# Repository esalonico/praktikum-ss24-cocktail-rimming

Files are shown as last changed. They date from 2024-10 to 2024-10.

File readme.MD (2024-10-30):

# Automated Cocktail Rimming System

**SS24 - Advanced Practical Course "Sustainable Process Automation: Humans, Software and the Mediator Pattern (IN2130, IN2106, IN4303)"**

An automated solution to streamline the process of rimming cocktail glasses, enhancing efficiency, consistency, and reducing resource waste, while at the same time praciting different skills like process management, 3D printing, electronics and process design/execution.

## Video

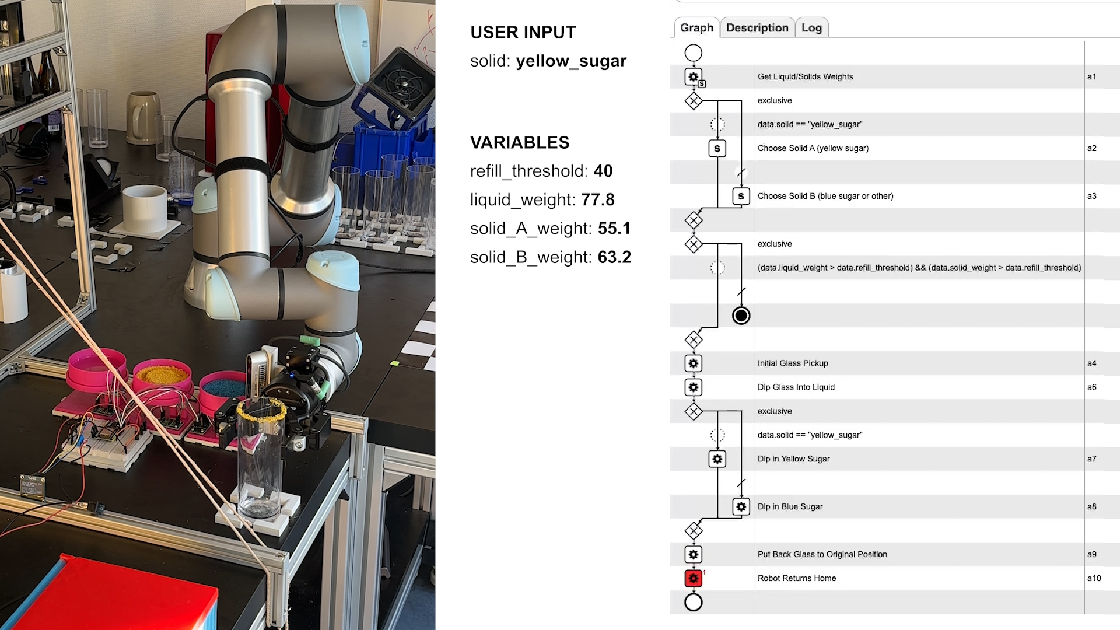
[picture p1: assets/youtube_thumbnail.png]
YouTube Video Thumbnail (https://youtu.be/M-wNSkutfYI)

*Click on the preview image to play the video on YouTube, or visit this URL: <https://youtu.be/M-wNSkutfYI>*

## Project Overview

### Main Idea

The goal of this project is to automate the process of rimming a cocktail glass. This involves dipping the glass first into a liquid (often lemon juice or syrups) and subsequently into a coating (such as sugar or salt) to enhance the presentation and flavor of the cocktail.

The project aims to solve the problem of manually rimming cocktail glasses by ensuring a consistent and efficient application of the sugar or salt coating. In practical use, this automation improves cocktail preparation times and minimizes waste by precisely controlling the amount of liquid and solid applied. Additionally, it provides the ability to track quantities used via integrated weighing sensors.

## Technical Summary

The project consists of three main components:

- **Robot**: From [Universal Robots](https://www.universal-robots.com/) for ultra precise and repeatable movements.
- **Hardware**: Custom-designed, 3D-printed components. *[(Go to section)](#hardware)*
- **Software**: Composed of CPEE (Cloud Process Execution Engine), ESP32 code, and a custom web server. *[(Go to section)](#software)*

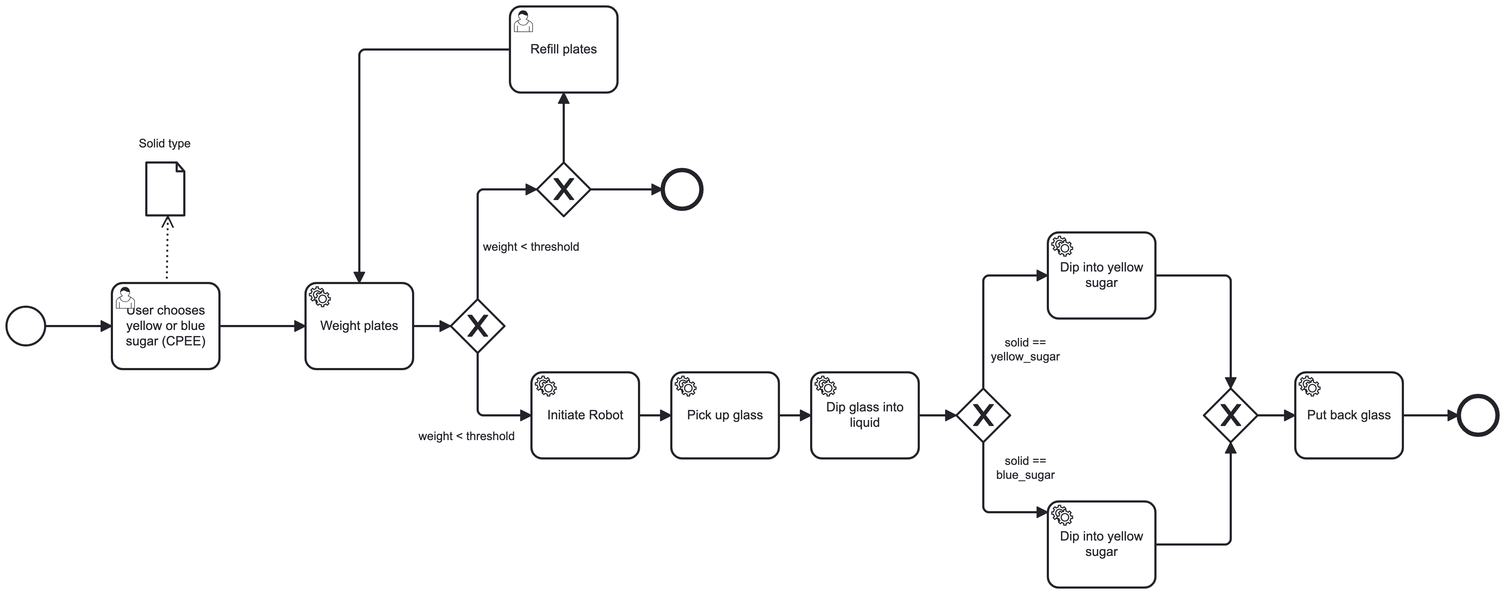
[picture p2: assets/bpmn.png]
BPMN
  
*High-level overview of the cocktail rimming process in BPMN.*

## Hardware

The hardware includes three identical stations to store and weigh the substances (one for the liquid and two for the solids). These stations connect to a central unit containing all circuits, the ESP32 microcontroller, an ON/OFF switch, and an OLED display.

This modular design facilitates straightforward scalability in the future.

### Components

- **In each station (3 total):**
  - **3D Printed Parts:**
    - Square base plate ([A](assets/3d_parts/A.stl))
    - Supports for the load cell ([B](assets/3d_parts/B.stl), [C](assets/3d_parts/B.stl))
    - Circular base plate (as a base for the plate) ([D](assets/3d_parts/D.stl))
    - Main plate (for storing liquid/solids) ([E](assets/3d_parts/E.stl))
  - **Electronics:**
    - 5kg load cell
    - HX711 amplifier
- **Control Center:**
  - ESP32 microcontroller (with WiFi support)
  - OLED I2C display
  - ON/OFF switch (connected to a 5V power adapter)

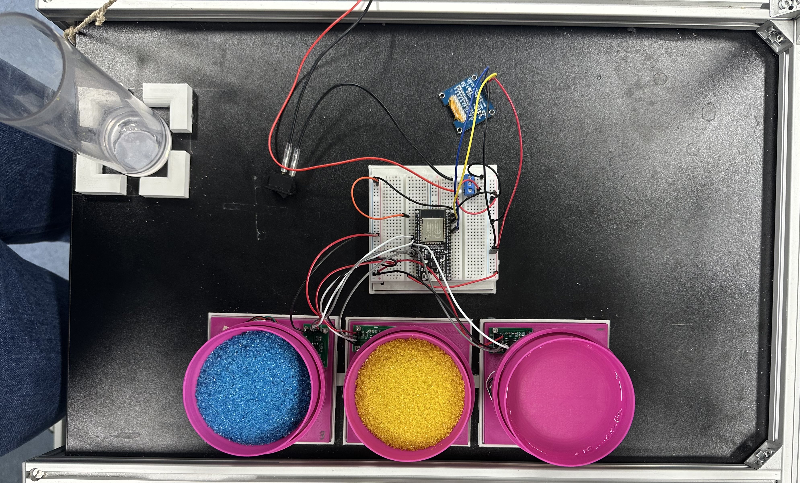
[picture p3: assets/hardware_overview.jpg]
Hardware Overview
  
*Hardware overview*

The custom 3D parts were designed using [Autodesk Fusion 360](https://www.autodesk.com/products/fusion-360/overview). Links to the `.stl` files for each component can be found above in the parts list.

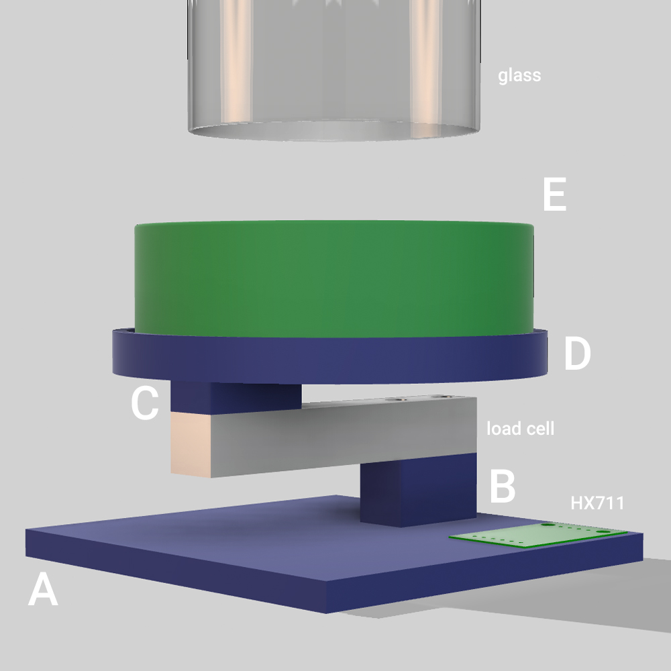
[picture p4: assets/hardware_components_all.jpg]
3D printed components
  
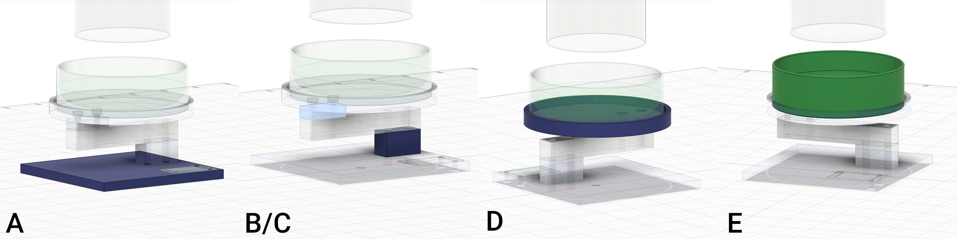
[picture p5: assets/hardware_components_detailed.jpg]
Detailed hardware components
  
*3D-printed hardware components.*

The design went through several iterations to find optimal solutions for various aspects such as load cell sensitivity, vibration motors to distribute sugar/salt (eventually discarded), and different plate sizes.

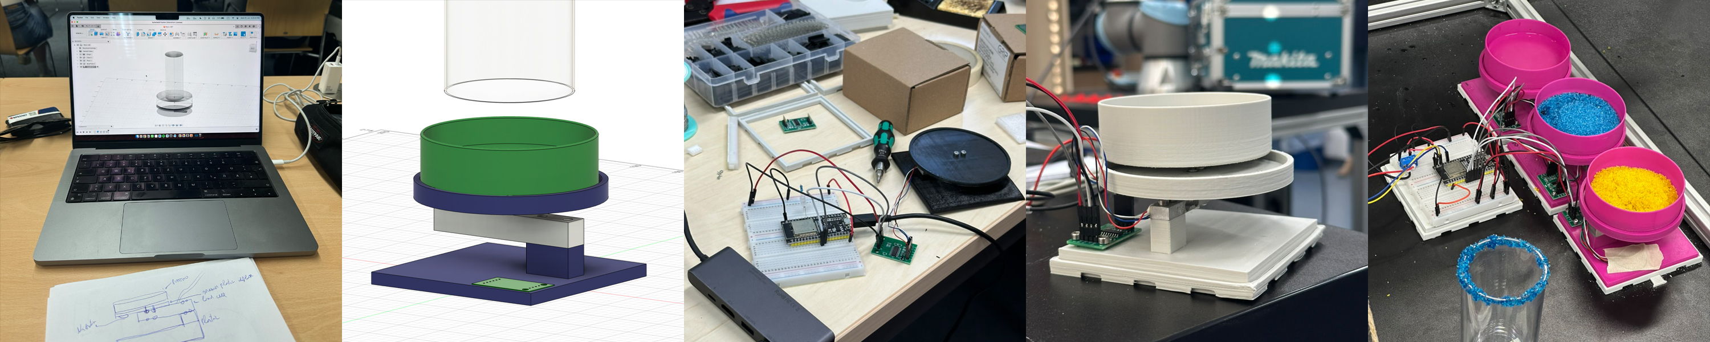
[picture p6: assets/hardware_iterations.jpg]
Iterations
  
*Multiple design iterations were necessary to achieve a working solution.*

Below is a diagram representation of the ESP32 pins and their connections.

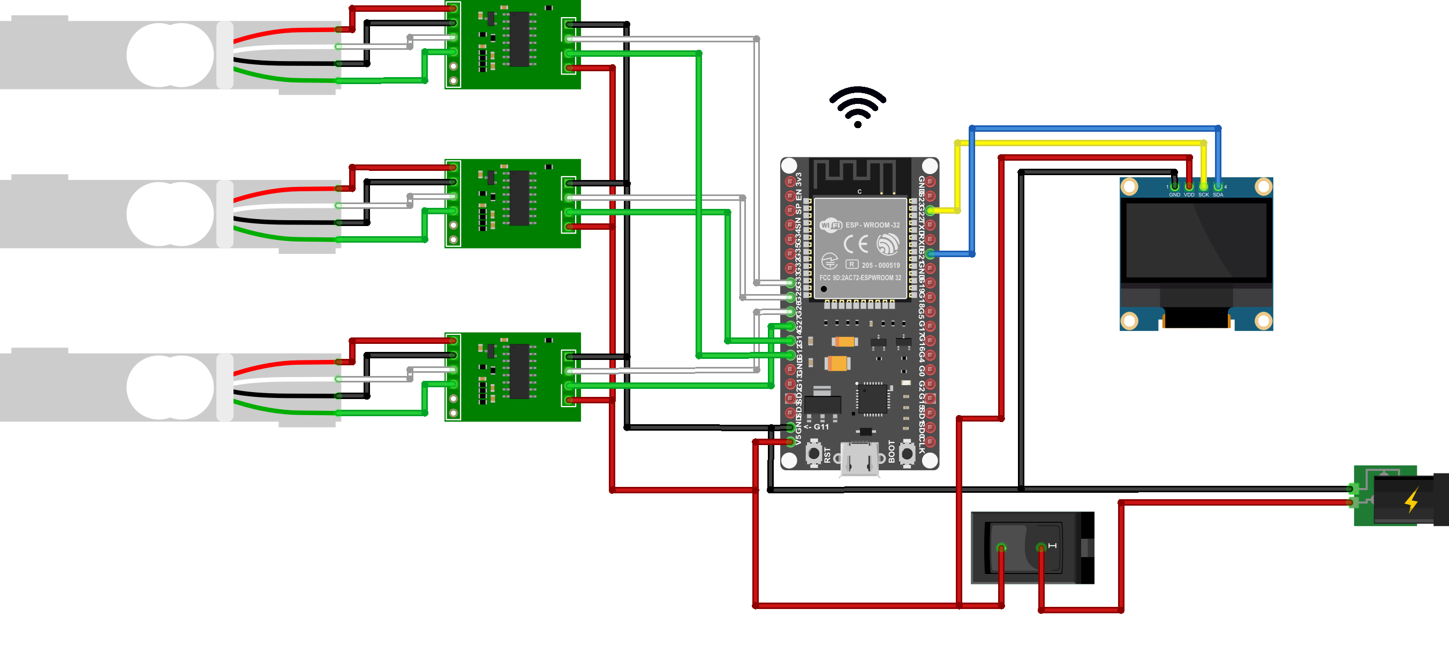
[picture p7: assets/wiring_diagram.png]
ESP32 Schematics
  
*Wiring diagram for the electronics connected to the ESP32.*

## Software

### Architecture

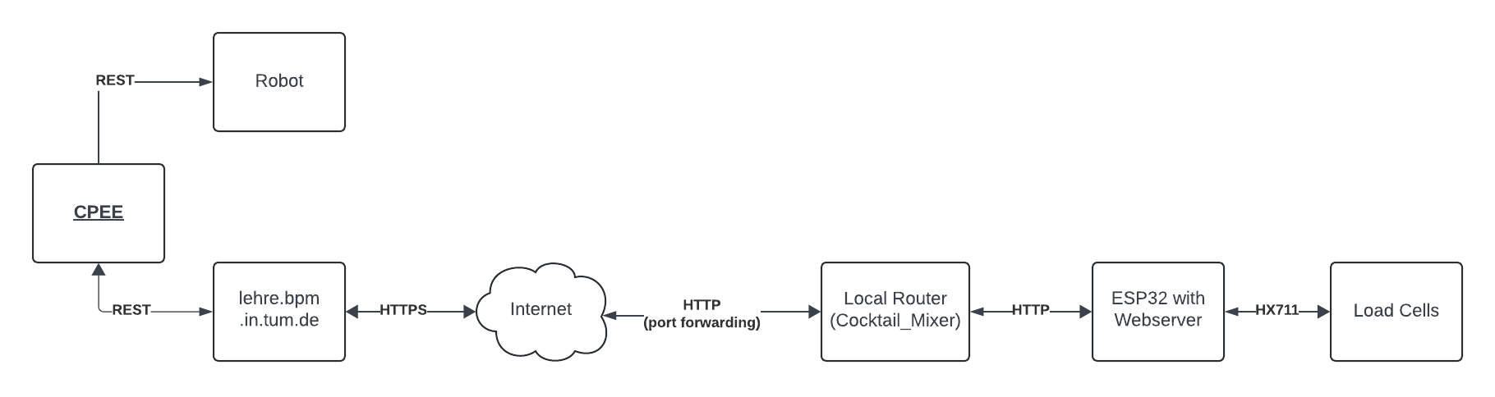
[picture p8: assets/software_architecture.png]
Architecture
  
*Architecture of all project components and their interactions.*

The software architecture includes the following main services:

- [**ESP32**](#esp-32): REST services between hardware and CPEE, web server, load cell configuration, and display management.
- [**CPEE**](#cpee-cloud-process-execution-engine): Process engine and orchestrator.
- **Robot**: Manages robotic actions to execute glass dipping sequences.
- [**WiFi Router**](#wifi-router): Makes the ESP32 web server accessible publicly.

#### ESP32

- **Purpose**: Provide a simple REST service to control and monitor the load cells (weight retrieval, status, calibration) and control the display (showing IP addresses for connecting to the web server).

The ESP32 uses an asynchronous web server (`AsyncWebServer`) to expose the routes. The endpoints are designed to guarantee isolation of data from the process, enabling them to be reused in various contexts with minimal dependencies.

##### API Documentation: GET `/weight`

- **Endpoint:**
  - **URL:** `{{WEBSERVER_IP}}/weight`
  - **Method:** `GET`
  - **Description:** Retrieves weight measurements (in grams) from all load cells connected to the ESP32 device.

##### **Response:**

- **Status Code:** `200 OK`
- **Content-Type:** `application/json`
- **Response Body:**
  
  ```json
  {
      "load_cells": [
          {
              "id": 1,
              "weight": 1.8
          },
          {
              "id": 2,
              "weight": 0.1
          },
          {
              "id": 3,
              "weight": 0.7
          }
      ]
  }
  ```

##### **Notes:**

- Replace `{{WEBSERVER_IP}}` with the IP address or domain name of the ESP32 web server.
- Weights are returned in grams with up to one decimal precision.

Additional routes are designed in `src/routes.cpp`. A Postman collection of all endpoints is available in [`assets/postman_collection.json`](assets/postman_collection.json).

Utilities for tasks such as load cell calibration, display testing, and HX711 debugging are available in the `utils` folder.

The project is built and managed via [PlatformIO](https://platformio.org/).

#### CPEE (Cloud Process Execution Engine)

- **Purpose**: Create a modular and well-structured process that coordinates the interactions between the user, sensors (load cells), and the robot.

Refer to the [video](#video) for a graphical representation of the process. Multiple CPEE components, such as service calls, script elements, and decisions, were used to fully utilize CPEE's capabilities.

#### WiFi Router

- **Purpose**: Expose the ESP32 web server endpoints to the internet.

Since modifying the routing configuration on eduroam is not possible, an additional router is used. The ESP32 connects to this router, which assigns a static local IP (192.168.0.125). Port forwarding is then set up to make port 80 accessible online, redirecting it to the ESP32's services.

The script [`utils/server_api.php`](utils/server_api.php) is used on the public server to forward requests to the ESP32.

## How to Run

- **ESP32 Setup:**
  - Create a file `data/wifi_credentials.txt` following the format in `data/SAMPLE_wifi_credentials.txt`.
  - In `main.cpp`, adjust:
    - Local IP address of the ESP32.
    - Public IP address or URL for accessing the web server.

- **Local Router Setup:**
  - Set up port forwarding for the ESP32's local IP address.

- **Public Server Setup:**
  - Upload `utils/server_api.php`.
  - Update the IP and port for the router.

## Challenges

### Personal Challenges

- Learning new skills including 3D modeling, 3D printing, soldering, electronics, and integrating these skills with robot commands.
- Optimizing the process engine based on lessons learned from the BPTM course.

### Technical Challenges

- Managing liquid and sugar refill (when below the threshold) using the robot.
- Ensuring even distribution of sugar/salt to avoid forming clumps (initially considered using a vibration motor).

## Future Implementations

- Use smaller load cells (e.g., less than 5kg) to better suit this application.
- Build an enclosure for the main unit.
- Add support for additional liquids/solids for a more modular design.
- Add debug/status displays for better monitoring.

---
**Author:** Emanuele Salonico | [emanuele.salonico@tum.de](mailto:emanuele.salonico@tum.de)

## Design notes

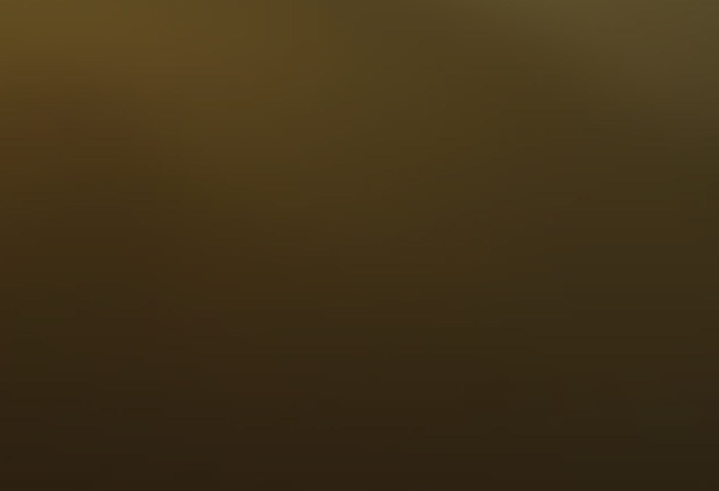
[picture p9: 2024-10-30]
assets/placeholder.png

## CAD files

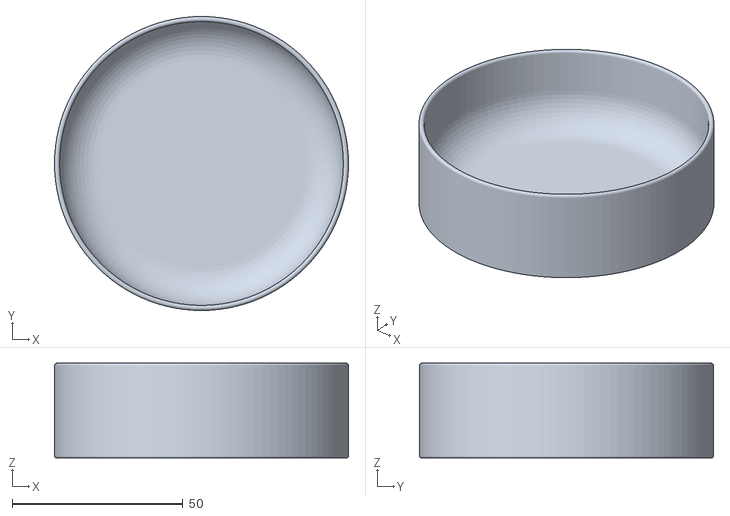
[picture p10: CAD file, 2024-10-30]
assets/3d_parts/E.stl
86.0 x 86.0 x 27.8

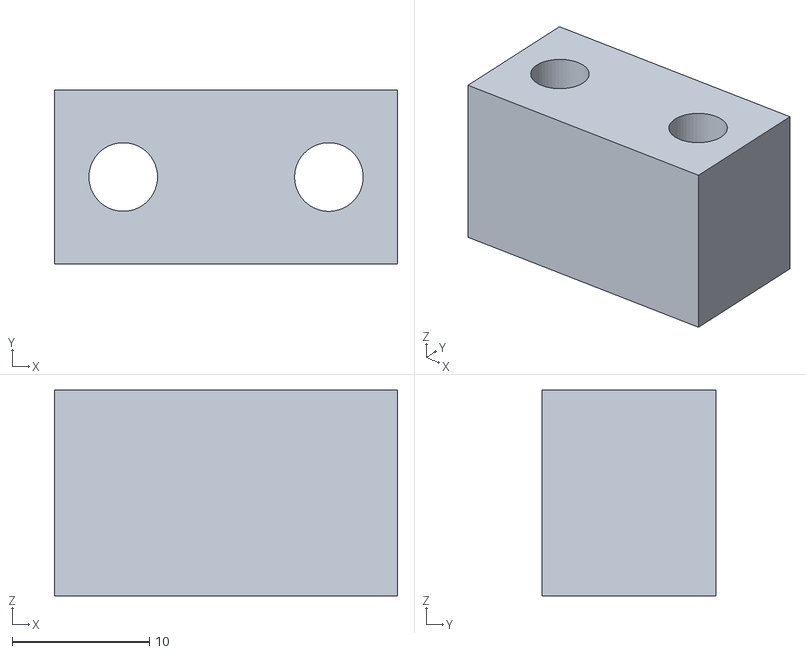
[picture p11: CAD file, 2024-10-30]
assets/3d_parts/B.stl
25.0 x 12.7 x 15.0

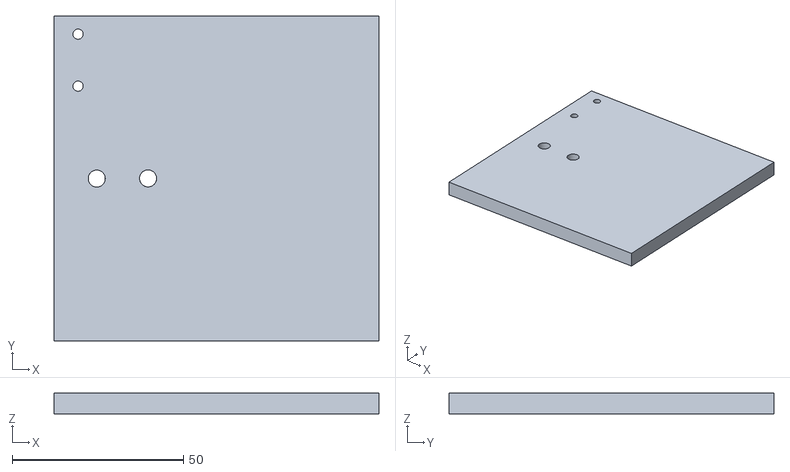
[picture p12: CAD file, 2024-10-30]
assets/3d_parts/A.stl
95.0 x 95.0 x 6.00

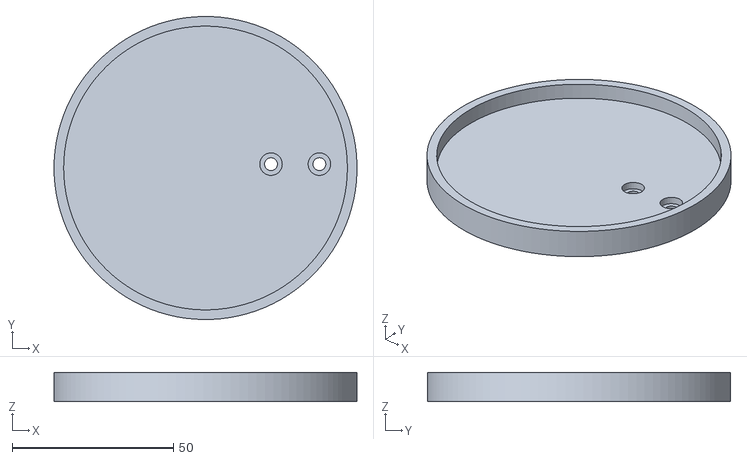
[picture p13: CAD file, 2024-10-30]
assets/3d_parts/D.stl
94.0 x 94.0 x 9.00

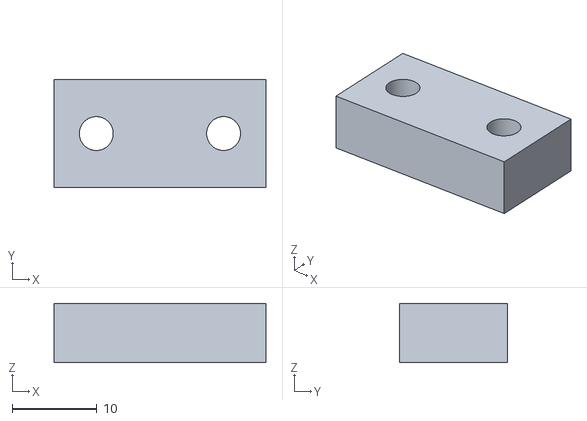
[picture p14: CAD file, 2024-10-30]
assets/3d_parts/C.stl
25.0 x 12.7 x 7.00

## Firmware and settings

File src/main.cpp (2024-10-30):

#include <Arduino.h>
#include <WiFi.h>
#include <AsyncTCP.h>
#include <ESPAsyncWebServer.h>
#include "FS.h"
#include "SPIFFS.h"
#include "HX711.h"
#include <Wire.h>
#include <Adafruit_GFX.h>
#include <Adafruit_SH1106.h>
#include "routes.h"

// Eduroam network credentials file path
const char *credentialsPath = "/wifi_credentials.txt";

// WiFi credentials
String ssid;
String password;

// WiFi network settings
IPAddress local_IP(192, 168, 0, 125); // Static IP
IPAddress gateway(192, 168, 0, 1);
IPAddress subnet(255, 255, 255, 0);

// Define the number of load cells
const int NUM_LOAD_CELLS = 3;

// HX711 instances
HX711 scales[NUM_LOAD_CELLS];

// Pins for each load cell (DOUT, SCK)
const int LOADCELL_PINS[NUM_LOAD_CELLS][2] = {
    {26, 27}, // Load cell 1: DOUT 26, SCK 27
    {25, 14}, // Load cell 2: DOUT 25, SCK 14
    {33, 12}  // Load cell 3: DOUT 33, SCK 12
};

// Calibration factors for each load cell
float calibration_factors[NUM_LOAD_CELLS] = {-410.0, -410.0, -380.0};

// Display setup
#define OLED_RESET 4
Adafruit_SH1106 display(OLED_RESET);

// Create instances of objects
HX711 scale;               // Create an instance of the HX711 class
AsyncWebServer server(80); // Create an AsyncWebServer object on port 80

// Function Prototypes
void readWiFiCredentials();
void initializeSerial();
void initializeDisplay();
void initializeScales();
void connectToWiFi();
void initializeServer();

// Function Implementations

void initializeSerial()
{
  // Initialize Serial Monitor
  Serial.begin(115200);
  delay(1000);
}

void initializeDisplay()
{
  // Initialize the OLED display at I2C address 0x3C
  display.begin(SH1106_SWITCHCAPVCC, 0x3C);
  display.clearDisplay();
  display.setTextSize(1);
  display.setTextColor(WHITE);
  display.setCursor(0, 0);
}

void initializeScales()
{
  for (int i = 0; i < NUM_LOAD_CELLS; ++i)
  {
    Serial.printf("Initializing scale %d...\n", i + 1); // TODO: remove
    scales[i].begin(LOADCELL_PINS[i][0], LOADCELL_PINS[i][1]);
    scales[i].set_scale();
    scales[i].tare();
    scales[i].set_scale(calibration_factors[i]);
  }
}

void readWiFiCredentials()
{
  if (!SPIFFS.begin(true))
  {
    Serial.println("An error occurred while mounting SPIFFS");
    return;
  }

  File file = SPIFFS.open(credentialsPath, "r");
  if (!file)
  {
    Serial.println("Failed to open credentials file");
    return;
  }

  ssid = file.readStringUntil('\n');
  ssid.trim();
  password = file.readStringUntil('\n');
  password.trim();

  file.close();

  // Debug output for credentials
  Serial.println("WiFi credentials read:");
  Serial.print("SSID: ");
  Serial.println(ssid);
}

void connectToWiFi()
{
  Serial.println("Connecting to Wi-Fi...");
  unsigned long startTime = millis();

  // Read WiFi credentials from SPIFFS
  Serial.println("Reading Wi-Fi credentials from SPIFFS");
  readWiFiCredentials();

  // Disconnect from any previous Wi-Fi connections
  Serial.println("Disconnecting from previous Wi-Fi connections");
  WiFi.disconnect(true);

  // Set Static IP address
  if (!WiFi.config(local_IP, gateway, subnet))
  {
    Serial.println("STA Failed to configure");
  }

  // Begin Wi-Fi connection
  Serial.printf("Connecting to SSID: %s\n", ssid.c_str());
  WiFi.begin(ssid, password);

  // Wait for connection
  while (WiFi.status() != WL_CONNECTED)
  {
    delay(500);
    Serial.print(".");
  }
  Serial.println("");
  Serial.println("Wi-Fi is connected!");
  Serial.print("IP address: ");
  Serial.println(WiFi.localIP());

  // Display IP address on OLED
  char buffer[50];
  sprintf(buffer, "Local IP address (%s):", ssid.c_str());
  display.println(buffer);
  display.println(WiFi.localIP().toString());
  display.println("\nPublic endpoint:");
  display.println("https://lehre.bpm.in.tum.de/~ge54bow/cocktail_rimming/api/");
  display.display();

  unsigned long duration = millis() - startTime;
  Serial.printf("Connected to Wi-Fi in %lu ms\n", duration);
}

void initializeServer()
{
  // Initialize server routes
  Serial.println("Initializing server...");
  setupRoutes(server, scales, NUM_LOAD_CELLS);

  // Start the server
  server.begin();
  Serial.println("Server started on port 80");
}

void setup()
{
  initializeSerial();
  initializeDisplay();
  initializeScales();
  connectToWiFi();
  initializeServer();
}

void loop()
{
  // No code needed here since we're using AsyncWebServer
}

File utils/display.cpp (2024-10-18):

/*********************************************************************
This is an example for our Monochrome OLEDs based on SSD1306 drivers

  Pick one up today in the adafruit shop!
  ------> http://www.adafruit.com/category/63_98

This example is for a 128x64 size display using I2C to communicate
3 pins are required to interface (2 I2C and one reset)

Adafruit invests time and resources providing this open source code, 
please support Adafruit and open-source hardware by purchasing 
products from Adafruit!

Written by Limor Fried/Ladyada  for Adafruit Industries.  
BSD license, check license.txt for more information
All text above, and the splash screen must be included in any redistribution
*********************************************************************/

/*********************************************************************
I change the adafruit SSD1306 to SH1106

SH1106 driver don't provide several functions such as scroll commands.

*********************************************************************/

#include <Arduino.h>
#include <SPI.h>
#include <Wire.h>
#include <Adafruit_GFX.h>
#include <Adafruit_SH1106.h>

#define OLED_RESET 4
Adafruit_SH1106 display(OLED_RESET);

#define NUMFLAKES 10
#define XPOS 0
#define YPOS 1
#define DELTAY 2


#define LOGO16_GLCD_HEIGHT 16 
#define LOGO16_GLCD_WIDTH  16 
static const unsigned char PROGMEM logo16_glcd_bmp[] =
{ B00000000, B11000000,
  B00000001, B11000000,
  B00000001, B11000000,
  B00000011, B11100000,
  B11110011, B11100000,
  B11111110, B11111000,
  B01111110, B11111111,
  B00110011, B10011111,
  B00011111, B11111100,
  B00001101, B01110000,
  B00011011, B10100000,
  B00111111, B11100000,
  B00111111, B11110000,
  B01111100, B11110000,
  B01110000, B01110000,
  B00000000, B00110000 };

#if (SH1106_LCDHEIGHT != 64)
#error("Height incorrect, please fix Adafruit_SH1106.h!");
#endif


void testdrawbitmap(const uint8_t *bitmap, uint8_t w, uint8_t h) {
  uint8_t icons[NUMFLAKES][3];
 
  // initialize
  for (uint8_t f=0; f< NUMFLAKES; f++) {
    icons[f][XPOS] = random(display.width());
    icons[f][YPOS] = 0;
    icons[f][DELTAY] = random(5) + 1;
    
    Serial.print("x: ");
    Serial.print(icons[f][XPOS], DEC);
    Serial.print(" y: ");
    Serial.print(icons[f][YPOS], DEC);
    Serial.print(" dy: ");
    Serial.println(icons[f][DELTAY], DEC);
  }

  while (1) {
    // draw each icon
    for (uint8_t f=0; f< NUMFLAKES; f++) {
      display.drawBitmap(icons[f][XPOS], icons[f][YPOS], logo16_glcd_bmp, w, h, WHITE);
    }
    display.display();
    delay(200);
    
    // then erase it + move it
    for (uint8_t f=0; f< NUMFLAKES; f++) {
      display.drawBitmap(icons[f][XPOS], icons[f][YPOS],  logo16_glcd_bmp, w, h, BLACK);
      // move it
      icons[f][YPOS] += icons[f][DELTAY];
      // if its gone, reinit
      if (icons[f][YPOS] > display.height()) {
	icons[f][XPOS] = random(display.width());
	icons[f][YPOS] = 0;
	icons[f][DELTAY] = random(5) + 1;
      }
    }
   }
}


void testdrawchar(void) {
  display.setTextSize(1);
  display.setTextColor(WHITE);
  display.setCursor(0,0);

  for (uint8_t i=0; i < 168; i++) {
    if (i == '\n') continue;
    display.write(i);
    if ((i > 0) && (i % 21 == 0))
      display.println();
  }    
  display.display();
}

void testdrawcircle(void) {
  for (int16_t i=0; i<display.height(); i+=2) {
    display.drawCircle(display.width()/2, display.height()/2, i, WHITE);
    display.display();
  }
}

void testfillrect(void) {
  uint8_t color = 1;
  for (int16_t i=0; i<display.height()/2; i+=3) {
    // alternate colors
    display.fillRect(i, i, display.width()-i*2, display.height()-i*2, color%2);
    display.display();
    color++;
  }
}

void testdrawtriangle(void) {
  for (int16_t i=0; i<min(display.width(),display.height())/2; i+=5) {
    display.drawTriangle(display.width()/2, display.height()/2-i,
                     display.width()/2-i, display.height()/2+i,
                     display.width()/2+i, display.height()/2+i, WHITE);
    display.display();
  }
}

void testfilltriangle(void) {
  uint8_t color = WHITE;
  for (int16_t i=min(display.width(),display.height())/2; i>0; i-=5) {
    display.fillTriangle(display.width()/2, display.height()/2-i,
                     display.width()/2-i, display.height()/2+i,
                     display.width()/2+i, display.height()/2+i, WHITE);
    if (color == WHITE) color = BLACK;
    else color = WHITE;
    display.display();
  }
}

void testdrawroundrect(void) {
  for (int16_t i=0; i<display.height()/2-2; i+=2) {
    display.drawRoundRect(i, i, display.width()-2*i, display.height()-2*i, display.height()/4, WHITE);
    display.display();
  }
}

void testfillroundrect(void) {
  uint8_t color = WHITE;
  for (int16_t i=0; i<display.height()/2-2; i+=2) {
    display.fillRoundRect(i, i, display.width()-2*i, display.height()-2*i, display.height()/4, color);
    if (color == WHITE) color = BLACK;
    else color = WHITE;
    display.display();
  }
}
   
void testdrawrect(void) {
  for (int16_t i=0; i<display.height()/2; i+=2) {
    display.drawRect(i, i, display.width()-2*i, display.height()-2*i, WHITE);
    display.display();
  }
}

void testdrawline() {  
  for (int16_t i=0; i<display.width(); i+=4) {
    display.drawLine(0, 0, i, display.height()-1, WHITE);
    display.display();
  }
  for (int16_t i=0; i<display.height(); i+=4) {
    display.drawLine(0, 0, display.width()-1, i, WHITE);
    display.display();
  }
  delay(250);
  
  display.clearDisplay();
  for (int16_t i=0; i<display.width(); i+=4) {
    display.drawLine(0, display.height()-1, i, 0, WHITE);
    display.display();
  }
  for (int16_t i=display.height()-1; i>=0; i-=4) {
    display.drawLine(0, display.height()-1, display.width()-1, i, WHITE);
    display.display();
  }
  delay(250);
  
  display.clearDisplay();
  for (int16_t i=display.width()-1; i>=0; i-=4) {
    display.drawLine(display.width()-1, display.height()-1, i, 0, WHITE);
    display.display();
  }
  for (int16_t i=display.height()-1; i>=0; i-=4) {
    display.drawLine(display.width()-1, display.height()-1, 0, i, WHITE);
    display.display();
  }
  delay(250);

  display.clearDisplay();
  for (int16_t i=0; i<display.height(); i+=4) {
    display.drawLine(display.width()-1, 0, 0, i, WHITE);
    display.display();
  }
  for (int16_t i=0; i<display.width(); i+=4) {
    display.drawLine(display.width()-1, 0, i, display.height()-1, WHITE); 
    display.display();
  }
  delay(250);
}

/*void testscrolltext(void) {
  display.setTextSize(2);
  display.setTextColor(WHITE);
  display.setCursor(10,0);
  display.clearDisplay();
  display.println("scroll");
  display.display();
 
  display.startscrollright(0x00, 0x0F);
  delay(2000);
  display.stopscroll();
  delay(1000);
  display.startscrollleft(0x00, 0x0F);
  delay(2000);
  display.stopscroll();
  delay(1000);    
  display.startscrolldiagright(0x00, 0x07);
  delay(2000);
  display.startscrolldiagleft(0x00, 0x07);
  delay(2000);
  display.stopscroll();
}*/
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

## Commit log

2024-10-21 added sample wifi credentials file
2024-10-30 proper readme and documentation
    [A.stl, B.stl, C.stl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]
